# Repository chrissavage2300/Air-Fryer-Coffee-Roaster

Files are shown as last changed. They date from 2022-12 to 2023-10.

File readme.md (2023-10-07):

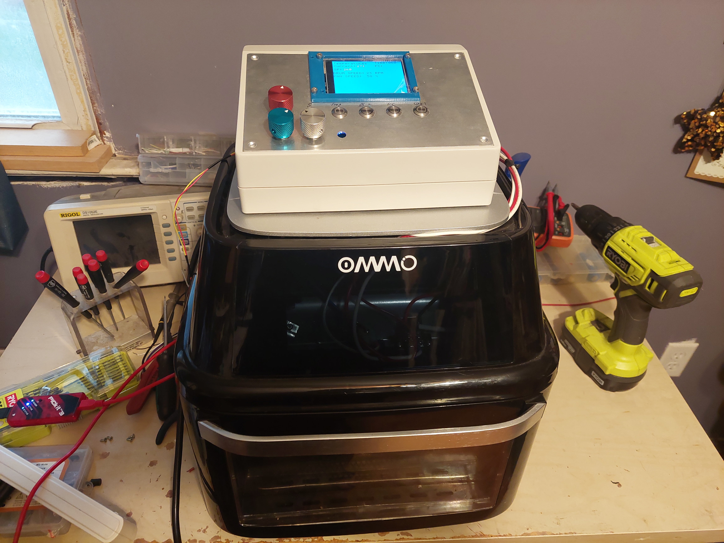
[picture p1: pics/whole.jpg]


A DIY Coffee roaster based on on air fryer. 

The idea is to have a rotating drum with a heater and fan inside. A nextion display will be used. 

Features:
Adjustable Temp
Adjustable Drum Speed
Adjustable Fan Speed
Cooling and heating modes

Change Log:

The roaster does work, but it has a slight issue when it gets hot where the rotation motor just doesnt turn. From what I can tell, its not a failure of the motor, but a fail in the comms. I have to look into why it does this, as i think its a buffer situation. Everything else works though, so Im not sure why just that gives out. 

10/7/2023- Uploaded Main Code

12/3/2022- Start of this github. But the project dates back a few months atleast

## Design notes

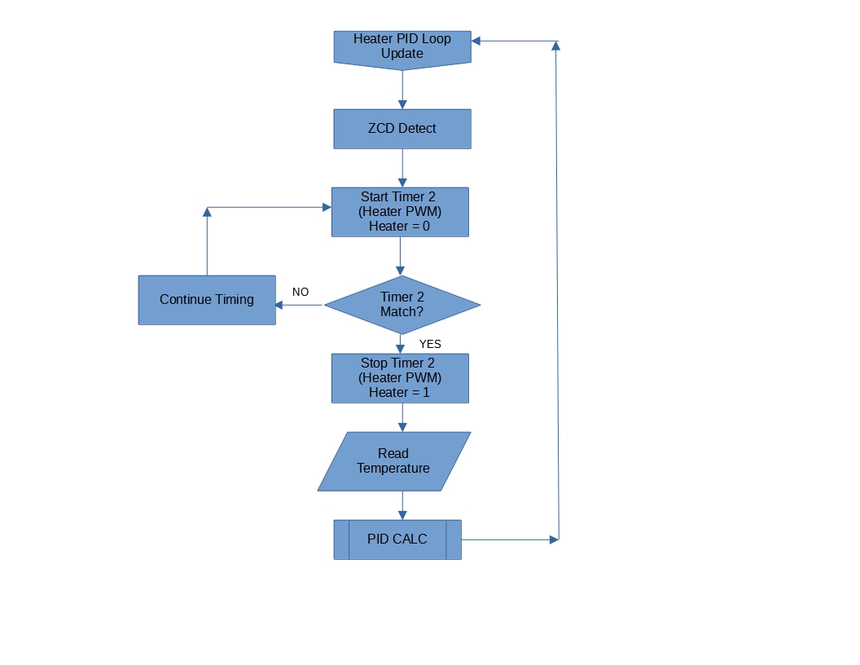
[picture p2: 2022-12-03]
code/ProgramFlowChart_2022_12_03_A_pg3.jpg

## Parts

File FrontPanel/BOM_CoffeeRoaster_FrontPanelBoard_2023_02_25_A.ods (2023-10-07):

Part | Value | Device | Package | Description
C1 | 22uF | CAP1206 | 1206 | Capacitor | CL31A226KPHNNNE/stock
C2 | 10uf | CAP1206 | 1206 | Capacitor | CL31A106KPHNNNE /stock
IC1 | AZ1117CR-3.3TRG1SOT89_AZ1117_DIO-M | AZ1117CR-3.3TRG1SOT89_AZ1117_DIO-M | SOT89_AZ1117_DIO-M |  | AZ1117CR-3.3TRG1/STOCK
IC2 | PIC16F18056-I/SO | PIC16F18056-I/SO | SOIC28-W_MC |  | STOCK
JP1 | DI | M08LOCK_LONGPADS | 1X08_LOCK_LONGPADS | Header 8 | ED10566-ND (https://www.digikey.com/en/products/detail/on-shore-technology-inc/OSTVN08A150/1588868)
JP2 | GLCD | M09LOCK-LONGPADS | 1X09_LOCK_LONGPADS | Header 9 | 2057-RS1-09-G-ND (https://www.digikey.com/en/products/detail/adam-tech/RS1-09-G/9832052)
JP4 | DO | M05LOCK_LONGPADS | 1X05_LOCK_LONGPADS | Header 5 | ED10564-ND (https://www.digikey.com/en/products/detail/on-shore-technology-inc/OSTVN05A150/1588865)
JP5 | ICSP | M05PTH | 1X05 | Header 5 | stock
JP6 | AI | M06LOCK_LONGPADS | 1X06_LOCK_LONGPADS | Header 6 | ED10565-ND (https://www.digikey.com/en/products/detail/on-shore-technology-inc/OSTVN06A150/1588866)
Q1 | MOSFET-NCHANNELBSS138 | MOSFET-NCHANNELBSS138 | SOT23-3 | Common NMOSFET Parts | IRLML6344TRPBF/STOCK
Q2 | MOSFET-NCHANNELBSS138 | MOSFET-NCHANNELBSS138 | SOT23-3 | Common NMOSFET Parts | IRLML6344TRPBF/STOCK
Q3 | MOSFET-NCHANNELBSS138 | MOSFET-NCHANNELBSS138 | SOT23-3 | Common NMOSFET Parts | IRLML6344TRPBF/STOCK
Q4 | MOSFET-NCHANNELBSS138 | MOSFET-NCHANNELBSS138 | SOT23-3 | Common NMOSFET Parts | IRLML6344TRPBF/STOCK
R1 | 10k | RESISTOR1206 | 1206 | Resistor | stock
R2 | 10k | RESISTOR1206 | 1206 | Resistor | stock
R3 | 10k | RESISTOR1206 | 1206 | Resistor | stock
R4 | 10k | RESISTOR1206 | 1206 | Resistor | stock
R5 | 10k | RESISTOR1206 | 1206 | Resistor | stock
R6 | 10k | RESISTOR1206 | 1206 | Resistor | stock
R7 | 10k | RESISTOR1206 | 1206 | Resistor | stock
R8 | 10k | RESISTOR1206 | 1206 | Resistor | stock
R9 | 10k | RESISTOR1206 | 1206 | Resistor | stock
R10 | 10k | RESISTOR1206 | 1206 | Resistor | stock
R11 | 50 | RESISTOR1206 | 1206 | Resistor | 47/STOCK
R12 | 50 | RESISTOR1206 | 1206 | Resistor | 47/STOCK
USARTIN |  | M04LONGPADS | 1X04_LONGPADS | Header 4 | ED10563-ND (https://www.digikey.com/en/products/detail/on-shore-technology-inc/OSTVN04A150/1588864)

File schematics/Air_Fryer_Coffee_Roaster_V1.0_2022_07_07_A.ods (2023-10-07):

 | Value | Device | Package | Description
BZ1 | CMI-1295-1285T | CMI-1295-1285T | CUI_CMI-1295-1285T | CUI Inc Buzzer Check availability | 102-CMI-1295-1285T-ND
C3 | 0.1uF | CAP0805 | 805 | Capacitor | 08055C104KAT4A/STOCK
C4 | 0.1uF | CAP0805 | 805 | Capacitor | 08055C104KAT4A/STOCK
C5 | 0.1u | CAP1206 | 1206 | Capacitor | CL31B104KBCNNNC/STOCK
C6 | 0.1u | CAP1206 | 1206 | Capacitor | CL31B104KBCNNNC/STOCK
C7 | 0.1u | CAP1206 | 1206 | Capacitor | CL31B104KBCNNNC/STOCK
C8 | 20uF,450V | CPOL-USE5-13 | E5-13 | POLARIZED CAPACITOR, American symbol | 450BXC22MEFC12.5X25
C9 | 270uF,16VDC | CAP_POLE | PANASONIC_E | Capacitor Polarized | EEE-HAE331UAP
C10 | 47uf | CAP_POLE | PANASONIC_E | Capacitor Polarized | EEE-1VA470P
C11 | 1nF,400VAC | C-US050-075X075 | C050-075X075 | CAPACITOR, American symbol | C907U102MYVDBA7317
D1 |  | DIODESOD-323F | SOD-323F | Diode | 1N4148WX-TP
D2 |  | DIODESOD-323F | SOD-323F | Diode | 1N4148WX-TP
F1 | 16A | FUSE | FUSE | FUSE | 696108003002 696122003001
HEATER_FAN | M025MM | M025MM | SCREWTERMINAL-5MM-2 | Standard 2-pin 0.1 | 1935161
IC1 | AZ1117C | ADP3338AKCZ-5-R7 | SOT230P700X180-4N | Low Dropout Regulator | AZ1117CH-5.0TRG1DICT-ND
IC2 | AZ1117CR-3.3TRG1 | AZ1117CR-3.3TRG1 | SOT89_AZ1117_DIO |  | AZ1117CR-3.3TRG1DICT-ND
IC3 | PIC16F18446-I/SOSOIC20_SO_MCH-M | PIC16F18446-I/SOSOIC20_SO_MCH-M | SOIC20_SO_MCH-M |  | stock
ISO1 | MOC3021SMOC3021S_LTO-M | MOC3021SMOC3021S_LTO-M | MOC3021S_LTO-M |  | MOC3021S
ISO2 | LTV-814S-TA1 | SFH6206 | DIL4-SMD | Optocoupler, Phototransistor Output, AC Input | LTV-814S-TA1
ISO4 | MOC3021SMOC3021S_LTO-M | MOC3021SMOC3021S_LTO-M | MOC3021S_LTO-M |  | MOC3021S
JP1 | ICSP | M05PTH | 1X05 | Header 5
JP2 |  | M02POLAR_LOCK | MOLEX-1X2_LOCK | Header 2
JP3 |  | M02POLAR_LOCK | MOLEX-1X2_LOCK | Header 2
JP5 | UART | M04LOCK | 1X04_LOCK | Header 4
L1 | 4.7uH, 2.2A | SRR1260-100M | IND_BOURNS_SRR1260 |  | NRS5040T4R7NMGK
LED1 | GRN | LED1206 | LED-1206 | LEDs | 732-4993-1-ND/ STOCK
LED2 | YELLOW | LED1206 | LED-1206 | LEDs | 732-4994-1-ND/STOCK
LED3 | GRN | LED1206 | LED-1206 | LEDs | 732-4993-1-ND/ STOCK
LED5 | BLUE | LED1206 | LED-1206 | LEDs | 732-4989-1-ND/STOCK
PIN | M025MM | M025MM | SCREWTERMINAL-5MM-2 | Standard 2-pin 0.1 | 1935161
POUT | M025MM | M025MM | SCREWTERMINAL-5MM-2 | Standard 2-pin 0.1 | 1935161
PS1 | LS05-13B12R3 | LS05-13B12R3 | CONV_LS05-13B12R3 |  | 2725-LS05-13B12R3-ND (https://www.digikey.com/en/products/detail/mornsun-america-llc/LS05-13B12R3/13531111)
Q1 | IRLML6344TRPBF | MOSFET-NCHANNEL2N7002PW | SOT323 | Common NMOSFET Parts | IRLML6344TRPBFCT-ND/ STOCK
Q2 | IRLML6344TRPBF | MOSFET-NCHANNEL2N7002PW | SOT323 | Common NMOSFET Parts | IRLML6344TRPBFCT-ND/ STOCK
Q3 | IRLML6344TRPBF | MOSFET-NCHANNEL2N7002PW | SOT323 | Common NMOSFET Parts | IRLML6344TRPBFCT-ND/ STOCK
R1 | 200 | R-US_R2512 | R2512 | RESISTOR, American symbol | CRM2512AJW-201ELFCT-ND
R2 | 6.19k | R-US_R2512 | R2512 | RESISTOR, American symbol | ERJ-1TNF6191U
R3 | 6.19k | R-US_R2512 | R2512 | RESISTOR, American symbol | ERJ-1TNF6191U
R4 | 220 | RESISTOR1206 | 1206 | Resistor | stock
R5 | 200 | R-US_R2512 | R2512 | RESISTOR, American symbol | CRM2512AJW-201ELFCT-ND
R6 | 220 | RESISTOR1206 | 1206 | Resistor | stock
R7 | 6.19k | R-US_R2512 | R2512 | RESISTOR, American symbol | ERJ-1TNF6191U
R8 | 10k | R-US_M0805 | M0805 | RESISTOR, American symbol | RNCP0805FTD10K0
R9 | 10k | R-US_M0805 | M0805 | RESISTOR, American symbol | RNCP0805FTD10K0
R10 | 340 | RESISTOR1206 | 1206 | Resistor
R15 | 2k | RESISTOR1206 | 1206 | Resistor | stock
R16 | 2k | RESISTOR1206 | 1206 | Resistor | stock
R19 | 340 | RESISTOR1206 | 1206 | Resistor
R20 | 10k | RESISTOR1206 | 1206 | Resistor | stock
T1 | BT138-600,127 | BT138-V | TO220BV | TRIAC | BT139-600E/DG,127
T2 | TRIACSMD | TRIACSMD | SOT223 |  | Z0107MN,135
TS1 | YK3210203000G | 282845-2 | CONN2_282845-2_TEC |  | YK3210203000G
U1 | MAX31855JASA | MAX31855JASA+21-0041B_8_MXM-M | 21-0041B_8_MXM-M

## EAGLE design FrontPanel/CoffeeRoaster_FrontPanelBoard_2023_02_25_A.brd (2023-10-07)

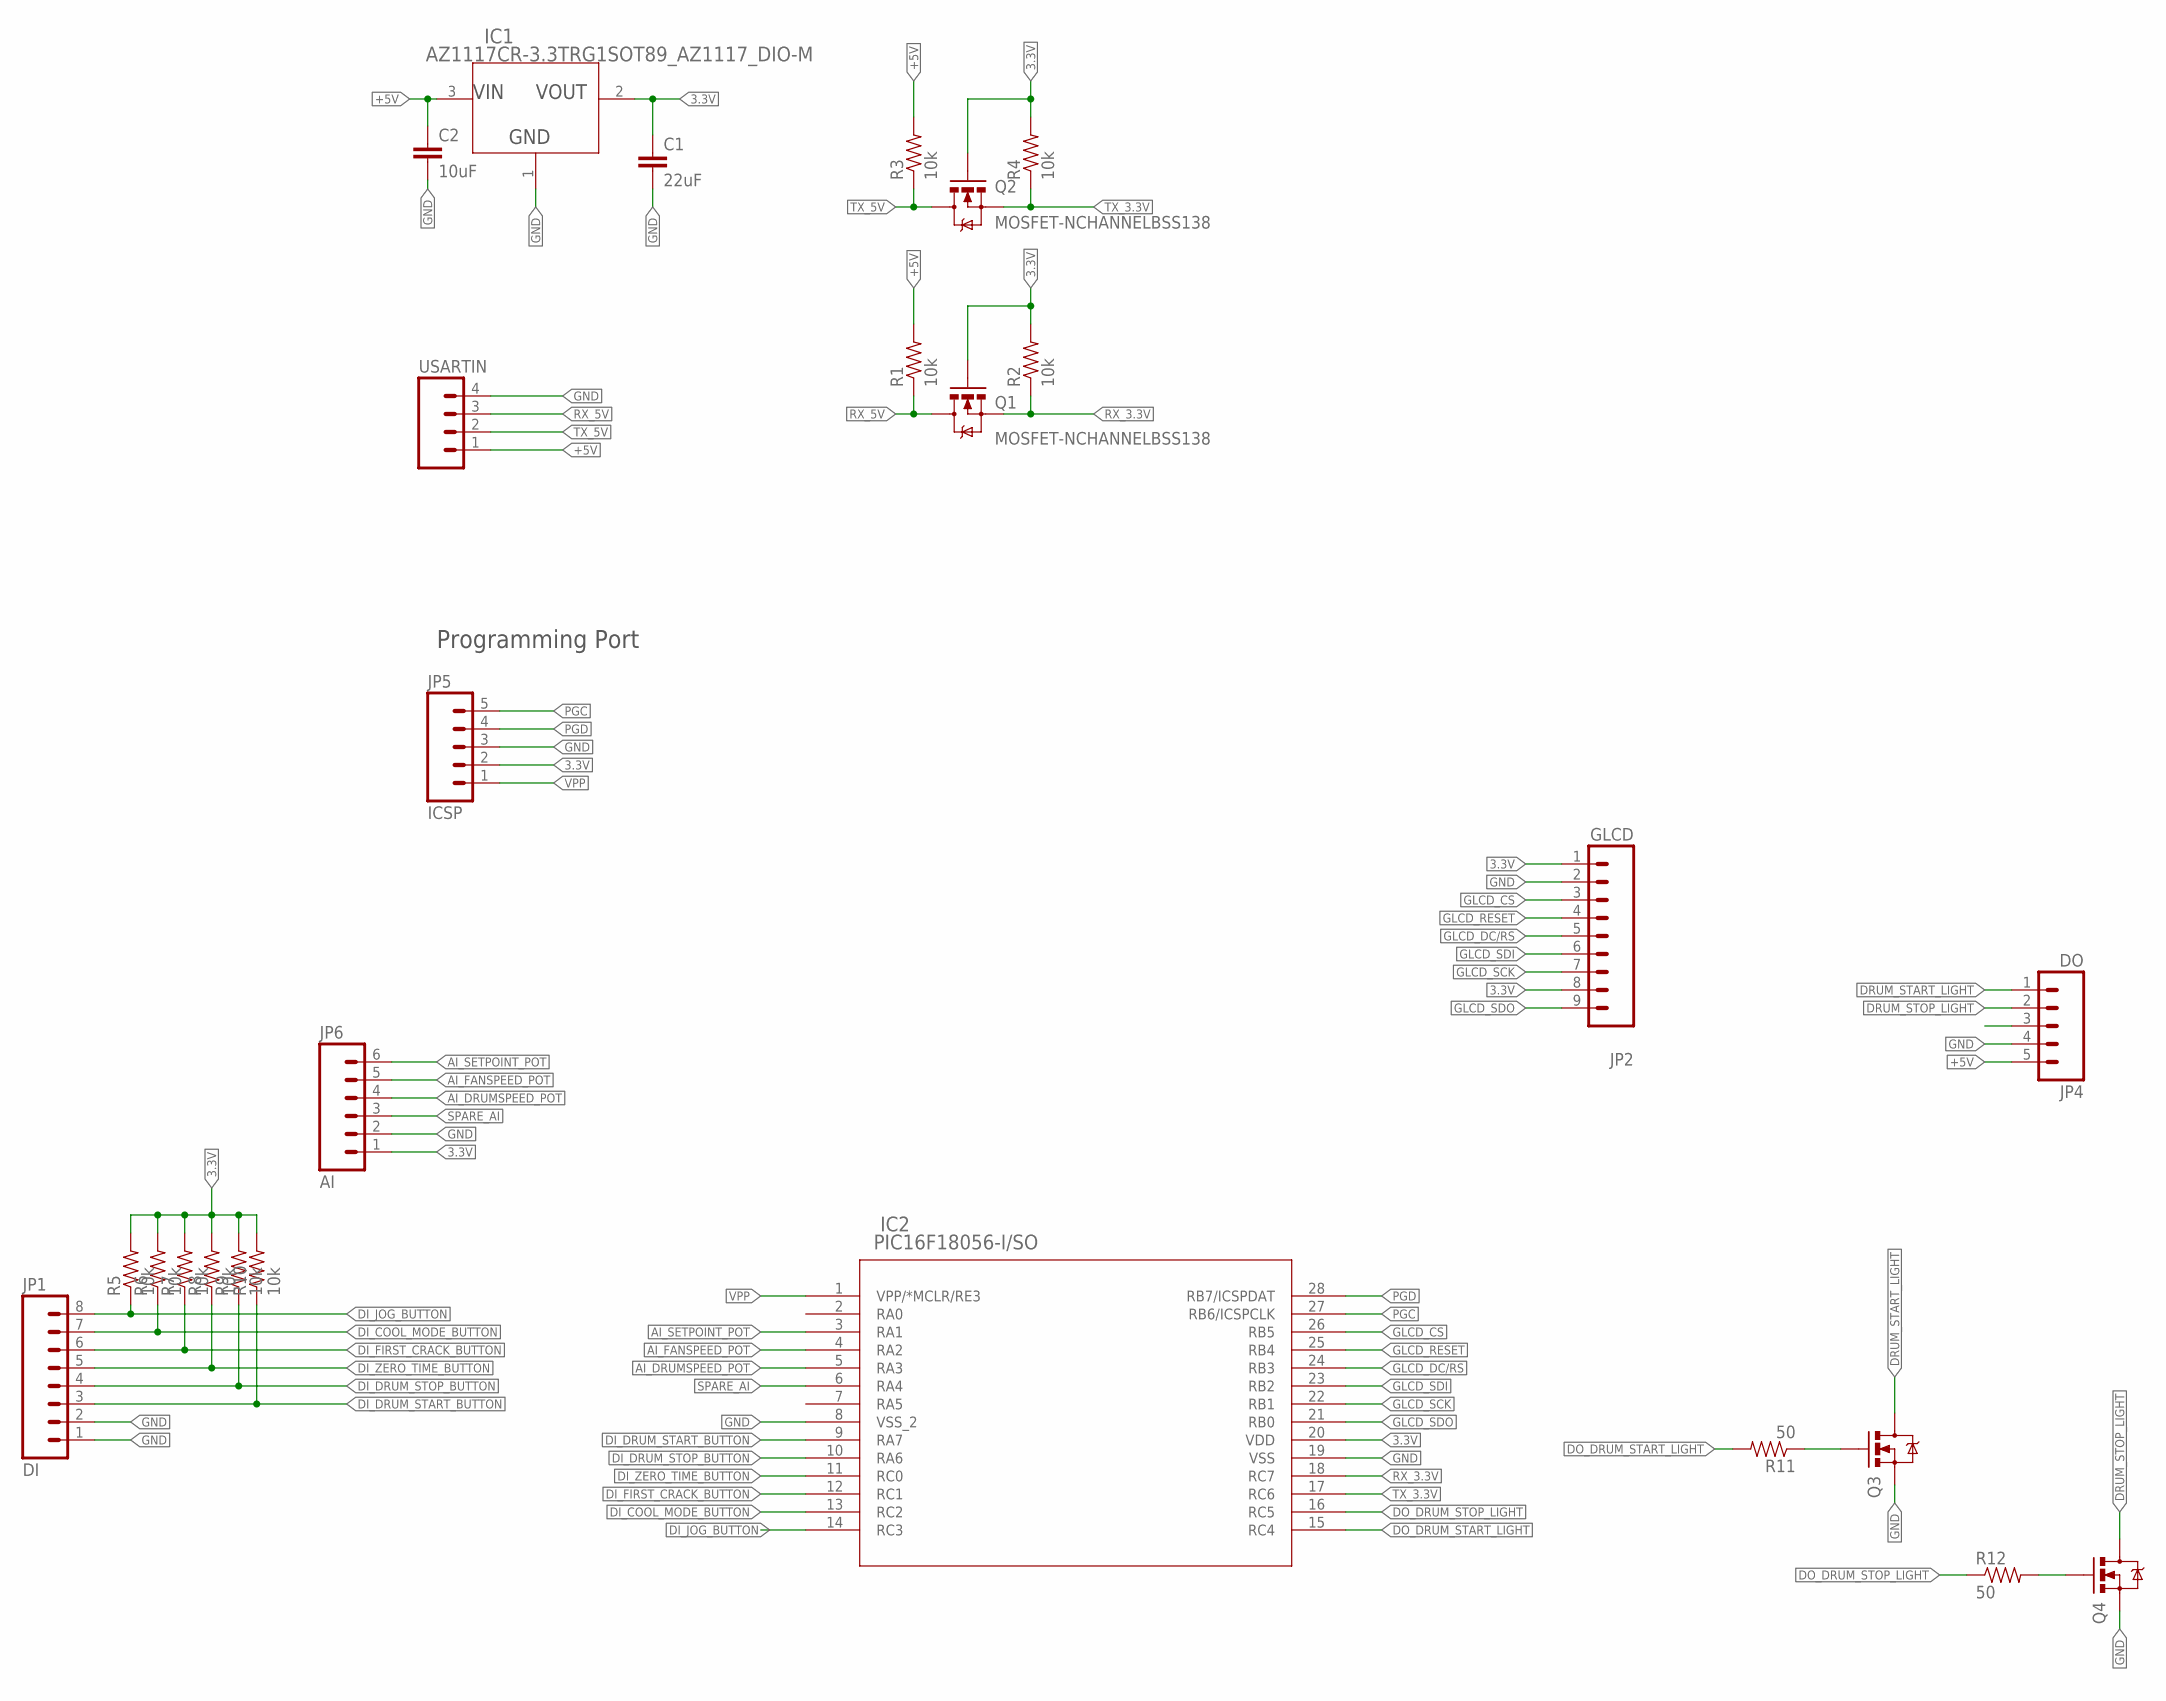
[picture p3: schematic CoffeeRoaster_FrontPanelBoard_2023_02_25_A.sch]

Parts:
C1: 22uF; 1206
C2: 10uF; 1206
IC1: AZ1117CR-3.3TRG1SOT89_AZ1117_DIO-M; SOT89_AZ1117_DIO-M
IC2: PIC16F18056-I/SO; SOIC28-W_MC
JP1: DI; 1X08_LOCK_LONGPADS
JP2: GLCD; 1X09_LOCK_LONGPADS
JP4: DO; 1X05_LOCK_LONGPADS
JP5: ICSP; 1X05
JP6: AI; 1X06_LOCK_LONGPADS
Q1, Q2, Q3, Q4: MOSFET-NCHANNELBSS138; SOT23-3
R1, R2, R3, R4, R5, R6, R7, R8, R9, R10: 10k; 1206
R11, R12: 50; 1206
USARTIN: M04LONGPADS; 1X04_LONGPADS

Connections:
3.3V: C1.1, IC1.2 (OUTPUT), IC2.20 (VDD), JP2.1, JP2.8, JP5.2, JP6.1, Q1.1 (G), Q2.1 (G), R2.2, R4.2, R5.2, R6.2, R7.2, R8.2, R9.2, R10.2
+5V: C2.1, IC1.3 (INPUT), JP4.5, R1.2, R3.2, USARTIN.1
AI_DRUMSPEED_POT: IC2.5 (RA3), JP6.4
AI_FANSPEED_POT: IC2.4 (RA2), JP6.5
AI_SETPOINT_POT: IC2.3 (RA1), JP6.6
DI_COOL_MODE_BUTTON: IC2.13 (RC2), JP1.7, R6.1
DI_DRUM_START_BUTTON: IC2.9 (RA7), JP1.3, R10.1
DI_DRUM_STOP_BUTTON: IC2.10 (RA6), JP1.4, R9.1
DI_FIRST_CRACK_BUTTON: IC2.12 (RC1), JP1.6, R7.1
DI_JOG_BUTTON: IC2.14 (RC3), JP1.8, R5.1
DI_ZERO_TIME_BUTTON: IC2.11 (RC0), JP1.5, R8.1
DO_DRUM_START_LIGHT: IC2.15 (RC4), R11.2
DO_DRUM_STOP_LIGHT: IC2.16 (RC5), R12.1
DRUM_START_LIGHT: JP4.1, Q3.3 (D)
DRUM_STOP_LIGHT: JP4.2, Q4.3 (D)
GLCD_CS: IC2.26 (RB5), JP2.3
GLCD_DC/RS: IC2.24 (RB3), JP2.5
GLCD_RESET: IC2.25 (RB4), JP2.4
GLCD_SCK: IC2.22 (RB1), JP2.7
GLCD_SDI: IC2.23 (RB2), JP2.6
GLCD_SDO: IC2.21 (RB0), JP2.9
GND: C1.2, C2.2, IC1.1 (ADJ/GND), IC2.8 (VSS_2), IC2.19 (VSS), JP1.1, JP1.2, JP2.2, JP4.4, JP5.3, JP6.2, Q3.2 (S), Q4.2 (S), USARTIN.4
unnamed: Q3.1 (G), R11.1
unnamed: Q4.1 (G), R12.2
PGC: IC2.27 (RB6/ICSPCLK), JP5.5
PGD: IC2.28 (RB7/ICSPDAT), JP5.4
RX_3.3V: IC2.18 (RC7), Q1.2 (S), R2.1
RX_5V: Q1.3 (D), R1.1, USARTIN.3
SPARE_AI: IC2.6 (RA4), JP6.3
TX_3.3V: IC2.17 (RC6), Q2.2 (S), R4.1
TX_5V: Q2.3 (D), R3.1, USARTIN.2
VPP: IC2.1 (VPP/*MCLR/RE3), JP5.1

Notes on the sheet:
Programming Port

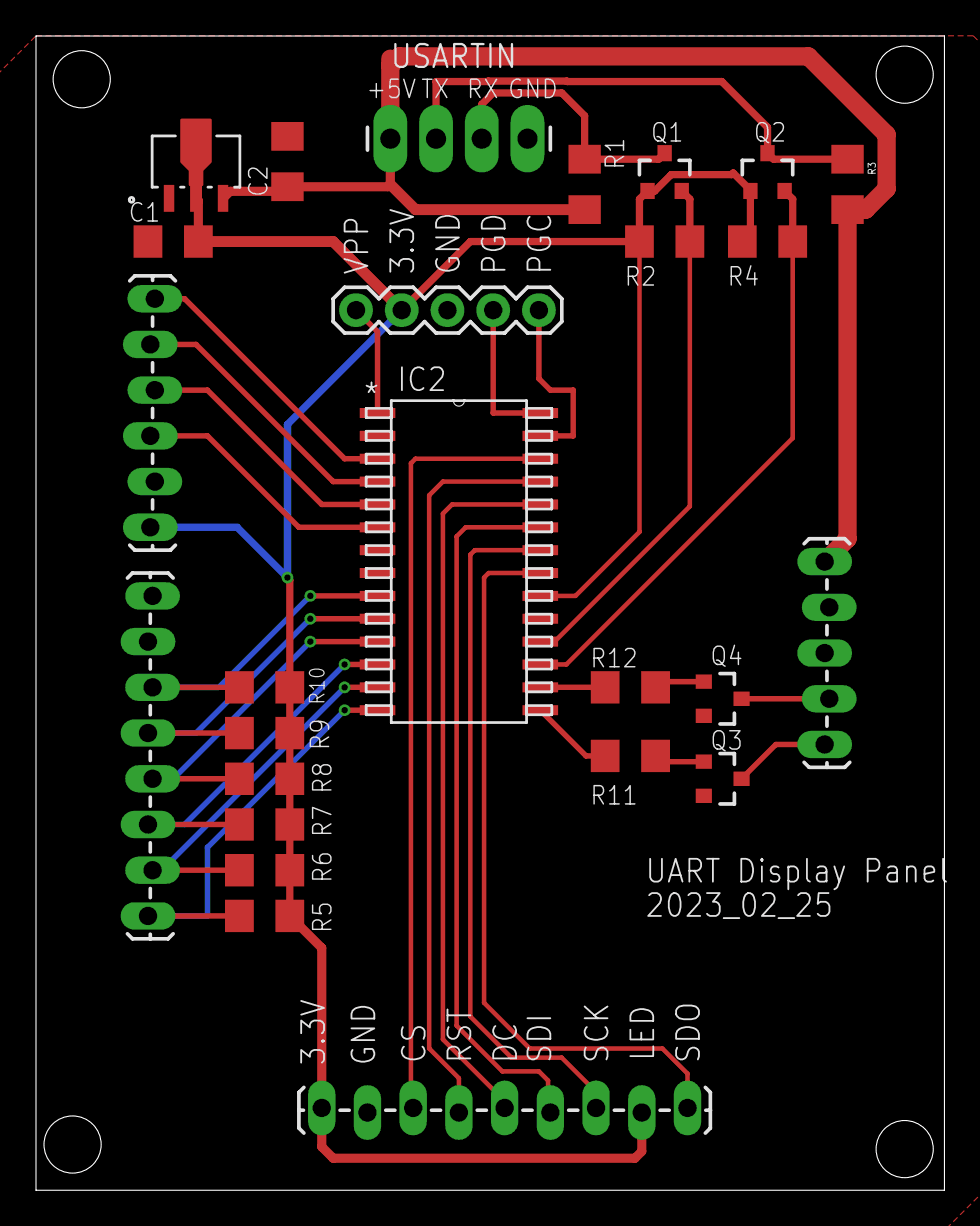
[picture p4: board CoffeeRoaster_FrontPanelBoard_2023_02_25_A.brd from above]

Board: 2 copper layers, 50.5 x 64.1 mm, 26 parts (0 on the bottom side), 32 nets.

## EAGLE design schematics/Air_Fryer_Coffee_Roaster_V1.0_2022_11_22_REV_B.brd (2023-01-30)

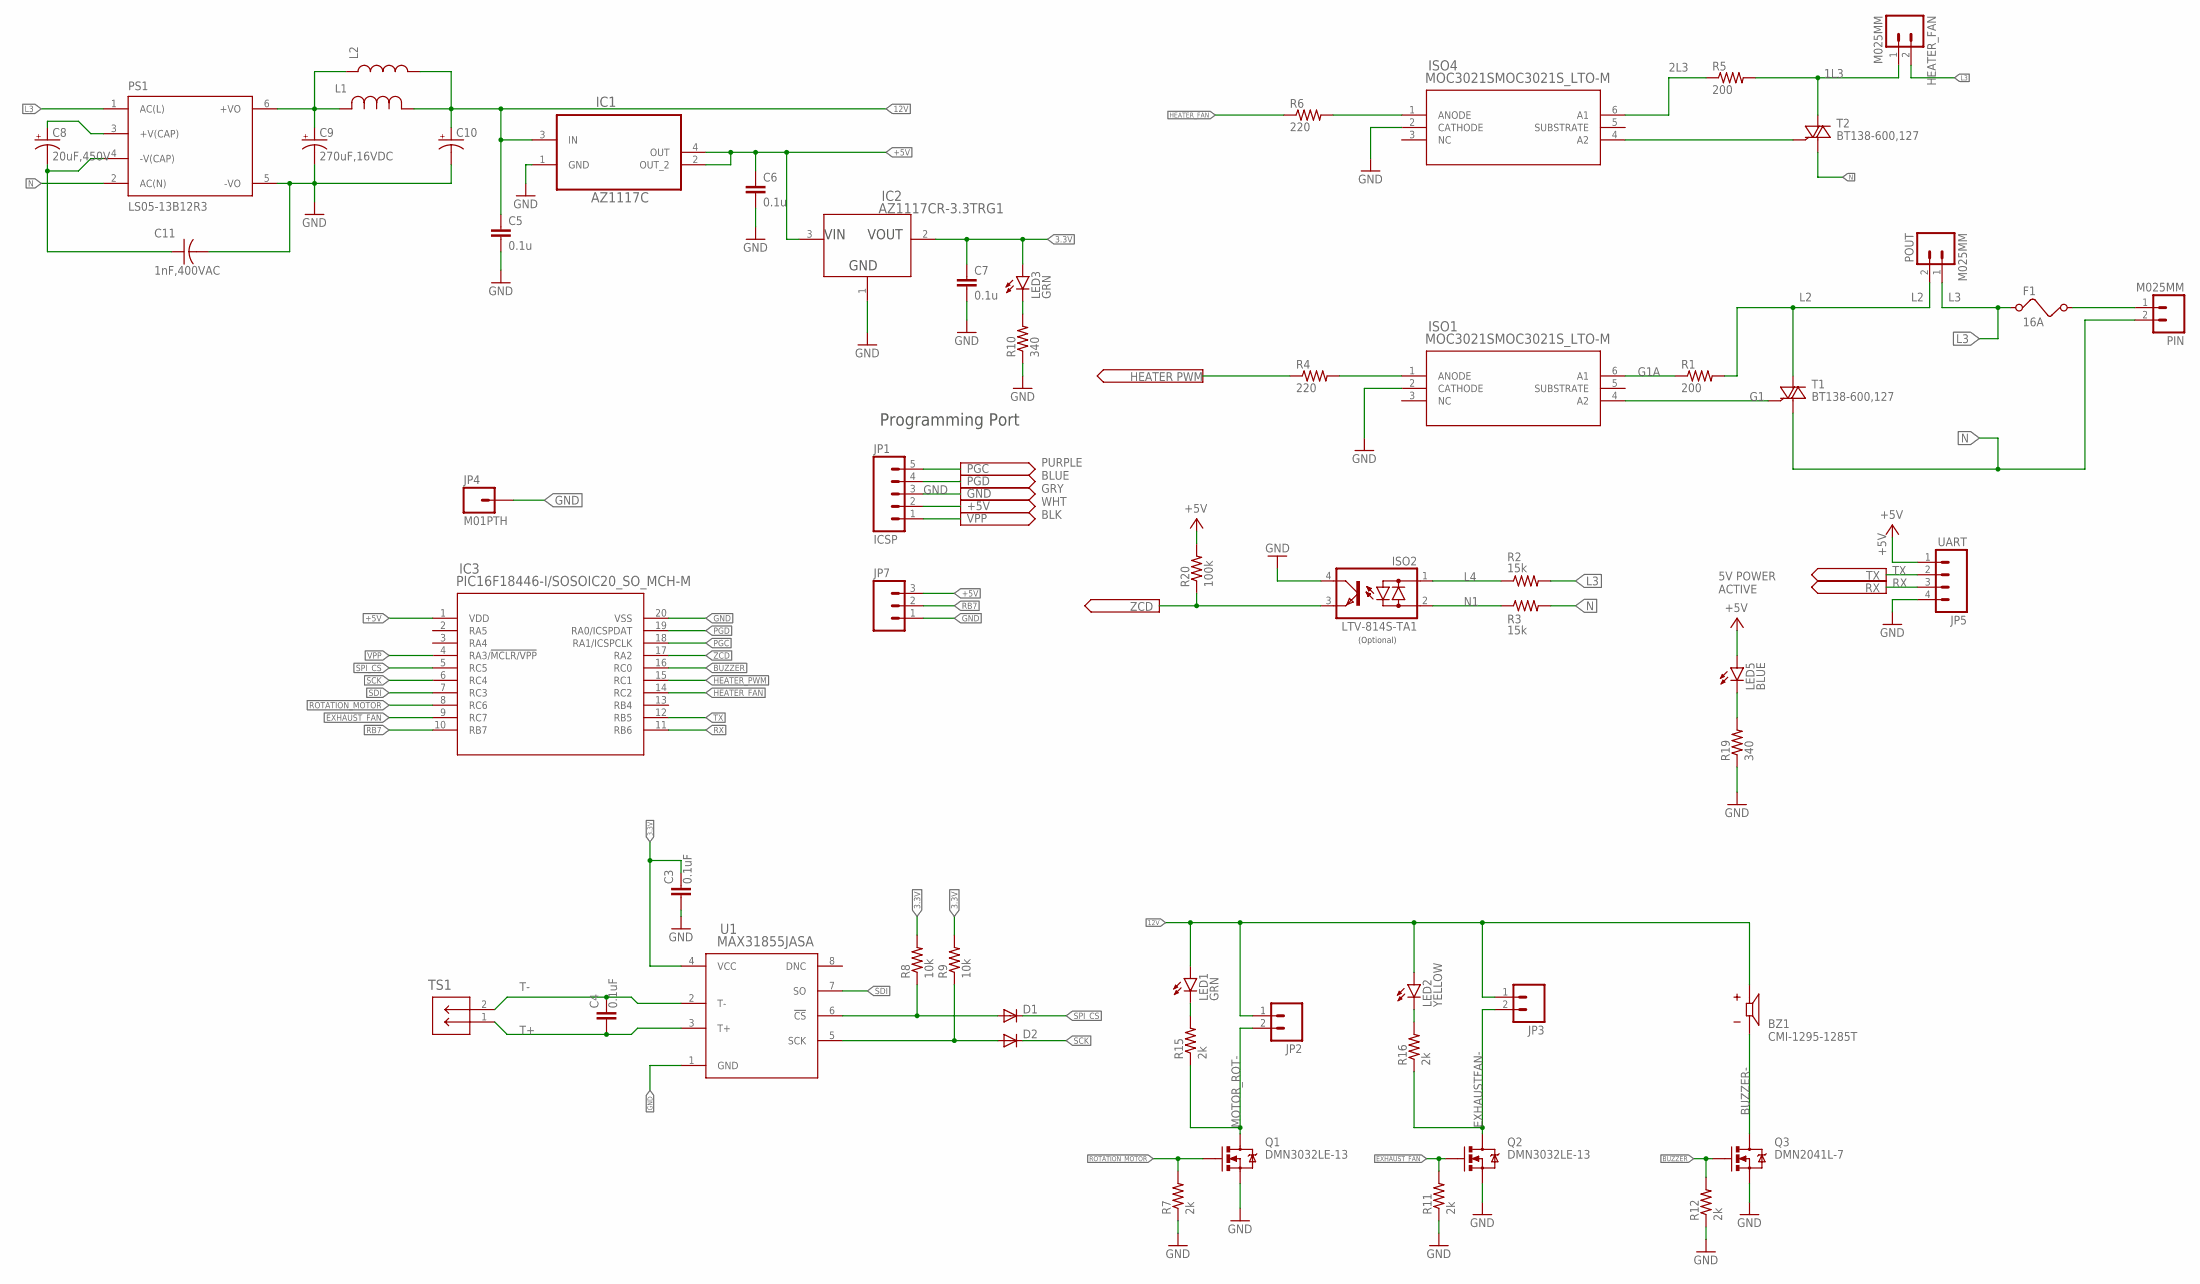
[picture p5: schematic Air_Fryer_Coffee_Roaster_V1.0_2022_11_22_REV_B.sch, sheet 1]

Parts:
BZ1: CMI-1295-1285T; CUI_CMI-1295-1285T
C3, C4: 0.1uF; 0805
C5, C6, C7: 0.1u; 1206
C8: 20uF,450V; E5-13
C9: 270uF,16VDC; PANASONIC_E
C10: CAP_POLE; PANASONIC_E
C11: 1nF,400VAC; C050-075X075
D1, D2: DIODESOD-323F; SOD-323F
F1: 16A; FUSE
HEATER_FAN: M025MM; SCREWTERMINAL-5MM-2
IC1: AZ1117C; SOT230P700X180-4N
IC2: AZ1117CR-3.3TRG1; SOT89_AZ1117_DIO
IC3: PIC16F18446-I/SOSOIC20_SO_MCH-M; SOIC20_SO_MCH-M
ISO1, ISO4: MOC3021SMOC3021S_LTO-M; MOC3021S_LTO-M
ISO2: LTV-814S-TA1; DIL4-SMD
JP1: ICSP; 1X05
JP2, JP3: M02POLAR_LOCK; MOLEX-1X2_LOCK
JP4: M01PTH; 1X01
JP5: UART; 1X04_LOCK
JP7: M03LOCK; 1X03_LOCK
L1: 4.7uH, 2.2A; IND_BOURNS_SRR1260
L2: INDUCTORCR54; CR54
LED1, LED3: GRN; LED-1206
LED2: YELLOW; LED-1206
LED5: BLUE; LED-1206
PIN: M025MM; SCREWTERMINAL-5MM-2
POUT: M025MM; SCREWTERMINAL-5MM-2
PS1: LS05-13B12R3; CONV_LS05-13B12R3
Q1, Q2: DMN3032LE-13; SOT223
Q3: DMN2041L-7; SOT23-3
R1, R5: 200; R2512
R2, R3: 15k; R2512
R4, R6: 220; 1206
R7, R11, R12, R15, R16: 2k; 1206
R8, R9: 10k; M0805
R10, R19: 340; 1206
R20: 100k; 1206
T1, T2: BT138-600,127; TO220BV
TS1: YK3210203000G; CONN2_282845-2_TEC
U1: MAX31855JASA; 21-0041B_8_MXM-M

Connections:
1L3: HEATER_FAN.1, R5.2, T2.T2 (A2)
2L3: ISO4.6 (A1), R5.1
3.3V: C3.2, C7.1, IC2.2 (OUTPUT), LED3.A, R8.2, R9.2, U1.4 (VCC)
12V: BZ1.P, C5.1, C10.+, IC1.3 (IN), JP2.1, JP3.1, L1.1, L2.P$2 (2), LED1.A, LED2.A
+5V: C6.1, IC1.2 (OUT_2), IC1.4 (OUT), IC2.3 (INPUT), IC3.1 (VDD), JP1.2, JP5.1, JP7.3, LED5.A, R20.2
BUZZER: IC3.16 (RC0), Q3.1 (G), R12.2
BUZZER-: BZ1.N, Q3.3 (D)
EXHAUSTFAN-: JP3.2, Q2.2 (D), Q2.4 (D), R16.1
EXHAUST_FAN: IC3.9 (RC7), Q2.1 (G), R11.2
G1: ISO1.4 (A2), T1.G
G1A: ISO1.6 (A1), R1.1
GATE_2: ISO4.4 (A2), T2.G
GND: C3.1, C5.2, C6.2, C7.2, C9.-, C10.-, C11.2, IC1.1 (GND), IC2.1 (ADJ/GND), IC3.20 (VSS), ISO1.2 (CATHODE), ISO2.4 (C), ISO4.2 (CATHODE), JP1.3, JP4.1, JP5.4, JP7.1, PS1.5 (-VO), Q1.3 (S), Q2.3 (S), Q3.2 (S), R7.1, R10.1, R11.1, R12.1, R19.1, U1.1 (GND)
HEATER_FAN: IC3.14 (RC2), R6.1
HEATER_PWM: IC3.15 (RC1), R4.1
L1: F1.2, PIN.1
L2: POUT.2, R1.2, T1.T2 (A2)
L3: F1.1, HEATER_FAN.2, POUT.1, PS1.1 (AC(L)), R2.2
L4: ISO2.1 (AC1), R2.1
MOTOR_ROT-: JP2.2, Q1.2 (D), Q1.4 (D), R15.1
N: PIN.2, PS1.2 (AC(N)), R3.2, T1.T1 (A1), T2.T1 (A1)
N1: ISO2.2 (AC2), R3.1
unnamed: ISO1.1 (ANODE), R4.2
unnamed: LED3.C, R10.2
unnamed: LED1.C, R15.2
unnamed: LED2.C, R16.2
unnamed: C8.+, PS1.3 (+V(CAP))
unnamed: C8.-, C11.1, PS1.4 (-V(CAP))
unnamed: ISO4.1 (ANODE), R6.2
unnamed: D1.A, R8.1, U1.6 (!CS)
unnamed: LED5.C, R19.2
unnamed: D2.A, R9.1, U1.5 (SCK)
unnamed: C9.+, L1.2, L2.P$1 (1), PS1.6 (+VO)
PGC: IC3.18 (RA1/ICSPCLK), JP1.5
PGD: IC3.19 (RA0/ICSPDAT), JP1.4
RB7: IC3.10 (RB7), JP7.2
ROTATION_MOTOR: IC3.8 (RC6), Q1.1 (G), R7.2
RX: IC3.11 (RB6), JP5.3
SCK: D2.C, IC3.6 (RC4)
SDI: IC3.7 (RC3), U1.7 (SO)
SPI_CS: D1.C, IC3.5 (RC5)
T+: C4.1, TS1.1, U1.3 (T+)
T-: C4.2, TS1.2, U1.2 (T-)
TX: IC3.12 (RB5), JP5.2
VPP: IC3.4 (RA3/!MCLR/VPP), JP1.1
ZCD: IC3.17 (RA2), ISO2.3 (E), R20.1

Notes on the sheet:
Programming Port
5V POWER ACTIVE
PURPLE BLUE GRY WHT BLK
(Optional)

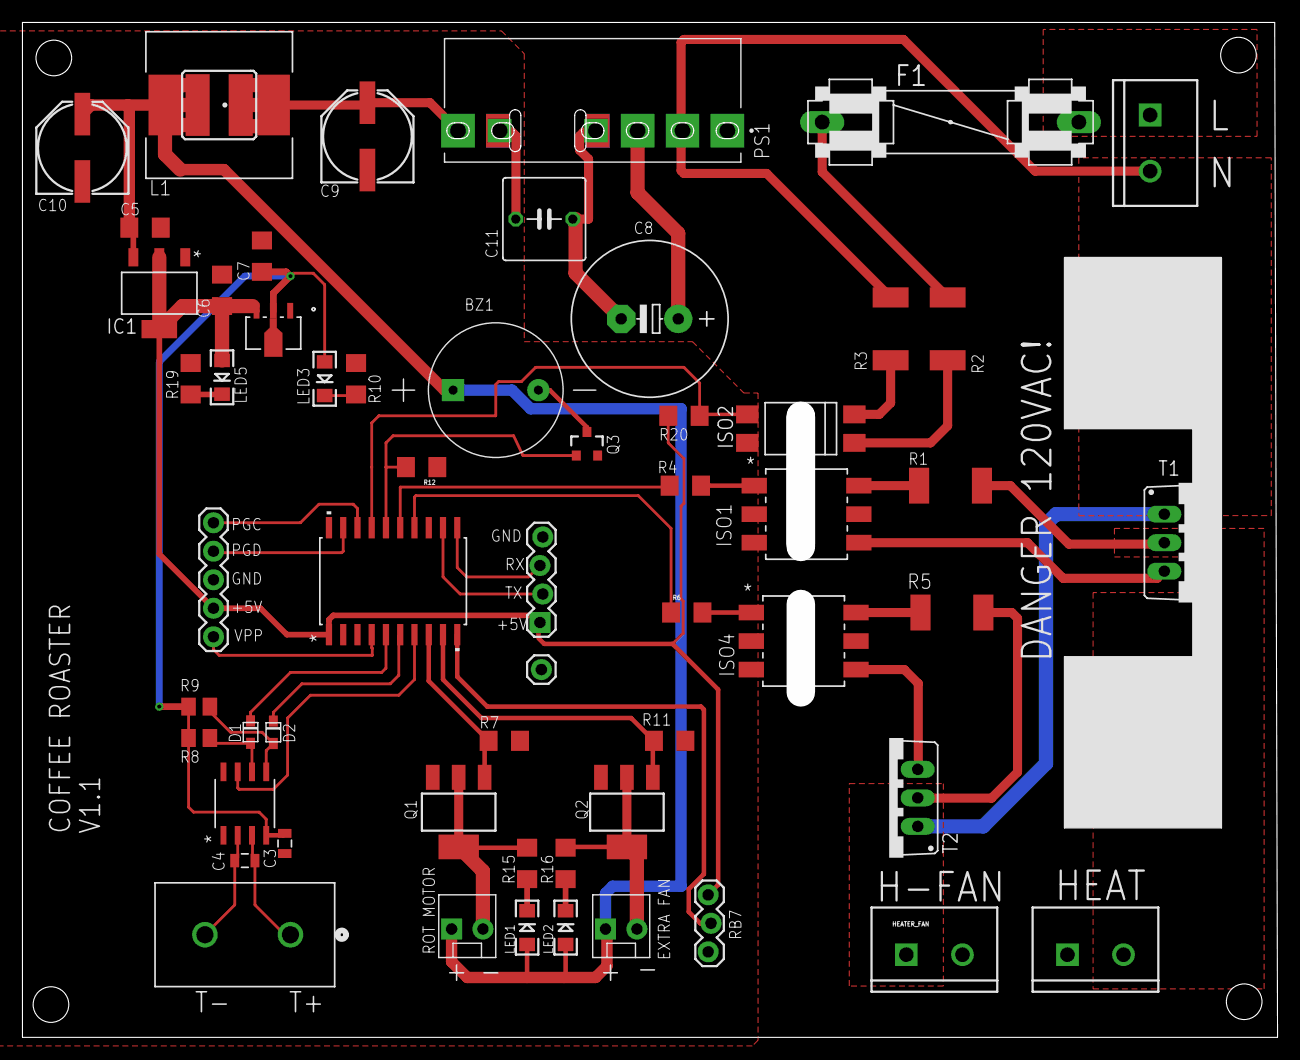
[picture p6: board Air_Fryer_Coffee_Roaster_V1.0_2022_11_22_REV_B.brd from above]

Board: 2 copper layers, 111.8 x 90.4 mm, 59 parts (0 on the bottom side), 46 nets.

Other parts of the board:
HEATSINK: 7-345-2PP-BA

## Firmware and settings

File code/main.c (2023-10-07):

/**
 * Coffee Roasting Control Board Software
 * 
 * 2023/02/10 
 * 
 * Heater Fan in Rev 1 is relay controlled
 * 
*/

#include "mcc_generated_files/mcc.h"
#include <stdio.h>
#include <string.h>


//SPI Vars
uint8_t writeData = 1; /* Data that will be transmitted */
uint8_t SPI_receiveData; /* Data that will be received */
uint8_t SPI_receiveData2;
uint8_t SPI_receiveData3;
uint8_t SPI_receiveData4;
unsigned int CurrentTemperature;
unsigned int TempVariable;
unsigned int ScaledTempF;
unsigned int ScaledTempHMI;

//PID loop vars
extern unsigned int DerivativeTime;  //external variable used in tmr1.c
signed int Intergral;
signed int Error;
//signed int PreviousError;
//signed char Derivative;
unsigned int SetTemperature;//
unsigned int PIDoutput;
unsigned int PIDinterm;
_Bool IntakeFanBit;

//PID control
extern unsigned char PID;
signed int ki_term;
signed int kp_term;


//make constants negative to invert output
//PID Constants
const signed int Kp = 12;//
const signed int Ki = 0;//
//const signed int Kd = 1;


//USART Vars
char buf[8];
extern uint8_t eusart1RxBuffer[8];
unsigned char COOL;
unsigned char HEAT;
unsigned char CLEARTIME;
unsigned char TEMP_MINUS;
unsigned char TEMP_PLUS;
unsigned char Fan_MINUS;
unsigned char Fan_PLUS;
unsigned char Rot_MINUS;
unsigned char Rot_PLUS;
unsigned char Rot_ON;
unsigned char Rot_OFF;
unsigned char FIRSTCRACK;

unsigned char NUMBERINPUT;
char IntBuffer[3];
unsigned int val;

unsigned char USART_TemperatureSP_Compare;
unsigned char USART_FanSPSP_Compare;
unsigned char USART_DrumSP_Compare;

//scaling vars
//PWM Scale calc: ((X * 2) + 745)/10 scales RPM input to PWM output
//PWM min = 76 (80%)), ~7RPM
//PWM max = 99 (100%), ~120 RPM
unsigned int RPM;
unsigned int RPM_Scaled;

//Fan Speed scaling
//Fan uses Timer 6
//160 is heater fan min
//0 is fully on
// therefore: (-1.6*X) + 160
//fanspeed is the requested speed. (0 to 100%))
//Fanspeed_scaled is the output to the timer
extern signed int Fanspeed=50;
extern unsigned char Fanspeed_Scaled;
unsigned char Old_Fanspeed;


//misc
extern unsigned int Elapsed_Time=0;//seconds
extern unsigned int Cooling_Time=0;//seconds
unsigned int Set_Time=1200;//seconds
extern _Bool RoastFinished=0;
extern _Bool CoolingMode=0;
extern _Bool CoolingSecondsBit=0;
unsigned char GarbageByte;
unsigned int StartupFinished=0;
extern unsigned char DisplayDelaytime=0;
unsigned int FirstCrackTime;

extern _Bool Overtemp;
extern _Bool ROTARTY_ON;

/*
                         Main application
 */

unsigned char PIDLoop(){//NOT USED CURRENTLY
    
//        //NOTE Higher values mean less of the sine wave gets passed
//        //PID = 0 is a full sine wave, PID = 255 is fully OFF
//        //IF INVERETED THIS IS REVERSE
//        //PIE3bits.RC1IE = 0;
//        Error = SetTemperature - ScaledTempHMI;
//        Intergral = Intergral + Error;
////        if (Error <=1){IntakeFanBit=1;EXHAUST_FAN_SetHigh();}//turn on the fan and bring in some fresh air
////        if (Error > 1){IntakeFanBit=0; EXHAUST_FAN_SetLow();}
//         //check Intergral error to make sure it doesnt get too large
//        if (Intergral >= 255){Intergral=255;}
//        if (Intergral <= -255){Intergral=-255;}            
//        
//        //Derivative = (Error - PreviousError)/DerivativeTime;
//        Derivative = (Error - PreviousError);   
//
//        
//        PIDoutput = (Error/Kp) + (Intergral*Ki) + (Derivative*Kd);            
//        //PIDoutput=~PIDoutput;
//        if (PIDoutput <= 0){PIDoutput=0;}
//        PreviousError = Error; 
//        return PIDoutput;   
//}


//Functions not used:
//void NextionBasic_command(char *Text) //basic command to get started.
//{
//    printf(Text);
//    EUSART1_Write(0xFF);
//    EUSART1_Write(0xFF);
//    EUSART1_Write(0xFF);
//    
//}
////This command sends a string and a number to a number box in the Nextion HMI
////so if you have a number box called "n0", the commands will be used like this:
////NextionSendNumber_command("n0.val=",i2);
////assuming i2 is an unsigned int
//void NextionSendNumber_command(char *Text,unsigned int number) 
//{
//        // disable receive interrupt
//    //PIE3bits.RC1IE = 0;
//    printf(Text);
//    printf("%d",number);
//    EUSART1_Write(0xFF);
//    EUSART1_Write(0xFF);
//    EUSART1_Write(0xFF);    
//        // enable receive interrupt
//    //PIE3bits.RC1IE = 1;
} 

void EUSART_Read_Text(char *Output, unsigned int length)
{
	unsigned int j;
	for(j=0;j<length;j++)
	Output[j] = EUSART1_Read();
}

void main(void)
{
    // initialize the device
    SYSTEM_Initialize();

    // Enable the Global Interrupts
    INTERRUPT_GlobalInterruptEnable();

    // Enable the Peripheral Interrupts
    INTERRUPT_PeripheralInterruptEnable();
        SPI1_Initialize();
        PWM6_Initialize();
                TMR2_Initialize();
        TMR2_Stop();

     
    PWM6EN=0;
    memset(buf,0,8);//clear buffer after
    SetTemperature = 450;
    //PIDoutput = 128;//set initial
    
    while (1)
    {
        



        //scale the RPM for the rotary drum.        
        RPM_Scaled = (((RPM*2)+746)/10);
        //This turns on and off the rotary drum
        //PWM6EN=1;//PWM6EN=0;
        PWM6_LoadDutyValue(RPM_Scaled);        
        Fanspeed_Scaled=(((Fanspeed*-10)+1600)/10);
       
        
        //MAX31885 notes: Last TWO bits of receiveData2 have to be dropped
        // in order to convert things. Then the number has to be multiplied by 0.25
        //OR shift to the right two times. 
        SPI1_Open(SPI1_DEFAULT);
        CS_SetLow();

        SPI_receiveData = SPI1_ExchangeByte(writeData);
        SPI_receiveData2 = SPI1_ExchangeByte(writeData);
        SPI_receiveData3 = SPI1_ExchangeByte(writeData);
        SPI_receiveData4 = SPI1_ExchangeByte(writeData);
        CS_SetHigh();
        SPI1_Close();
        TempVariable = SPI_receiveData2 | SPI_receiveData<<8;
        TempVariable = (TempVariable >> 2);
        CurrentTemperature = TempVariable/4;
        ScaledTempF = ((CurrentTemperature*18)+320)/10; //convert to F
        ScaledTempHMI=ScaledTempF;


        //this function stops the output from getting too high as an over temp shut off
        if (ScaledTempHMI > SetTemperature)
            {
            Overtemp=1;
            HEATER_PWM_SetLow();//Setting low turns OFF the SCR
            EXHAUST_FAN_SetHigh();
            TMR2_Stop();
        }
        if (ScaledTempHMI < SetTemperature) {

            EXHAUST_FAN_SetLow();
            Overtemp = 0;
            
            if (DerivativeTime==1){ //check to see if its time to do math
                Error = SetTemperature - ScaledTempHMI;
                
                //Intergral = Intergral + Error;

                //check Intergral error to make sure it doesnt get too large
                //not really using the integral
                //if (Intergral >= 1023){Intergral=1023;}
                //if (Intergral <= -1023){Intergral=-1023;}           
                //Derivative = (Error - PreviousError);   

                //ki_term = (Intergral*Ki);
                kp_term = (Error*Kp);

                PIDoutput = kp_term; //+            

                if (PIDoutput <= 0){PIDoutput=0;}
                if (PIDoutput >=1000){PIDoutput=1000;}
                //PreviousError = Error;


                  //scale the output. In practice the min output for any physical change to happen is 150               
                 //PID=255-((PIDoutput*25)/100);
                 PIDinterm=((PIDoutput*16)/100);
                 PID = 160-PIDinterm;//
                 DerivativeTime=0;
                }//PID loop

        }     
   


        
        if (RoastFinished==0){

        }//roast NOT finished loop
        
        if (DisplayDelaytime==1 && RoastFinished == 0){
                
            // uncomment these lines
            printf("t");
            printf("%0.3u",Elapsed_Time);
           // __delay_ms(10);
            printf("a");
            printf("%0.3u",ScaledTempHMI);            
            //printf("%0.3u",ScaledTempHMI);    
             DisplayDelaytime=0;
         //PID=PIDLoop();
        }
        
        
        
        if (Elapsed_Time==Set_Time){//do times match? If so shut off heater
            //PID=255;
            HEATER_PWM_SetHigh();
            //Fanspeed=100;
            TMR2_Stop();
            //TMR1_StopTimer();                               
            //CoolingMode=1;
            //Cooling_Time=0;
            //RoastFinished=1;
            //Elapsed_Time=0;
            
        }//Roast Finished loop
        if (CoolingMode==1 && CoolingSecondsBit==1){

            //PID=255;
            HEATER_PWM_SetHigh();
            //Fanspeed=100;
            TMR2_Stop();
            RoastFinished=1;
            //Elapsed_Time=0;
            CoolingSecondsBit=0;
            DerivativeTime=0;
            
            //RPM=75;
        }//cooling mode loop    
        
    
    if (eusart1RxCount!=0){//is RX count not equal to 0? (ie is it 1)
     //begin sequence to read from the serial port
     //EUSART_Read_Text(buf,6);
     //make a button that prints out "FAN"
     //then compare and look for it

        
        EUSART_Read_Text(buf,4);
        //EUSART1_Write("0");
        COOL = strncmp (buf,"XCOL",4);
        //cooling mode on
        if (COOL==0){

         CoolingMode=1;

         memset(buf,0,8);//clear buffer after
        }

        CLEARTIME = strncmp (buf, "XZER",4);
        if (CLEARTIME==0){
          Elapsed_Time=0;
          printf("t");
          printf("%0.3u",Elapsed_Time);
          memset(buf,0,8);//clear buffer after
        }
        
        FIRSTCRACK = strncmp (buf, "XFCZ",4);
        if (FIRSTCRACK==0){
            FirstCrackTime=Elapsed_Time;
            //printf("z");
            //printf("%u",FirstCrackTime);
            Elapsed_Time=0;
            printf("t");
            printf("%0.3u",Elapsed_Time);
            
          memset(buf,0,4);//clear buffer after
        }        
//        TEMP_PLUS = strncmp (buf, "TE+",3);
//        if (TEMP_PLUS==0){
//            SetTemperature=SetTemperature+5;
//            //printf("Current Set Point Changed: =%u\n",SetTemperature);
//          memset(buf,0,3);//clear buffer after
//        }
//        //adjust Fan Speed
//        Fan_MINUS = strncmp (buf, "FE-",3);
//        if (Fan_MINUS==0){
//            Fanspeed=Fanspeed-5;
//            //printf("Current speed Changed: =%u\n",Fanspeed);
//          memset(buf,0,3);//clear buffer after
//        }        
//        Fan_PLUS = strncmp (buf, "FE+",3);
//        if (Fan_PLUS==0){
//            Fanspeed=Fanspeed+5;
//            //printf("Current speed Changed: =%u\n",Fanspeed);
//          memset(buf,0,3);//clear buffer after
//        }
//        //adjust rotation speed
//        Rot_MINUS = strncmp (buf, "RO-",3);
//        if (Rot_MINUS==0){
//            RPM=RPM-5;
//            //printf("Current Rotation Changed: =%u\n",RPM);
//          memset(buf,0,3);//clear buffer after
//        }        
//        Rot_PLUS = strncmp (buf, "RO+",3);
//        if (Rot_PLUS==0){
//            RPM=RPM+5;
//            //printf("Current Rotation Changed: =%u\n",RPM);
//            memset(buf,0,3);//clear buffer after
//        }
        Rot_ON = strncmp(buf, "XRON",4);
        if (Rot_ON==0){
            PWM6EN=1;
            ROTARTY_ON=1;
            //printf("Rotation ON\n");
            memset(buf,0,8);//clear buffer after           
        }
        Rot_OFF = strncmp(buf, "XROF",4);
        if (Rot_OFF==0){
            PWM6EN=0;
            ROTARTY_ON=0;
            //printf("Rotation OFF\n");
            memset(buf,0,8);//clear buffer after           
        }

    //command structure from display:
    //Snnn = temperature set point, character "S" followed by the 3 digits
    //Fnnn = Fan speed set point, character "F" followed by the 3 digits
    //Dnnn = Drum Speed set point, character "D" followed by the 3 digits
    //this then converts the number to ASCII and then we print
    //First function looks for temp set point    
        USART_TemperatureSP_Compare = strncmp(buf,"S",1);

        if (USART_TemperatureSP_Compare==0)
        {
            //memset(buf,0,3); //clear only the first 3 bytes
            //move things into a new buffer so we can get rid of the leading zeros
            IntBuffer[0]=buf[1];
            IntBuffer[1]=buf[2];
            IntBuffer[2]=buf[3];
            //then convert the buffer to an int;
            
            //***TEMP REMOVED ///***
            SetTemperature=atoi(IntBuffer);
            //then spit it back out in another text box. 
            //NextionSendNumber_command("n0.val=",val);
            //printf("New Setpoint: =%u\n",SetTemperature);
            //printf("I see you\n");
            memset(buf,0,4); //then clear the buffer after use
            memset(IntBuffer,0,4);
        }//end Set Point Look up
        
        //Look for Fan Speed Set Point
        
        USART_FanSPSP_Compare = strncmp(buf,"F",1);
        
        if (USART_FanSPSP_Compare ==0)
        {
            IntBuffer[0]=buf[1];
            IntBuffer[1]=buf[2];
            IntBuffer[2]=buf[3];
            Fanspeed=atoi(IntBuffer);
            //("New Fan Speed: =%u\n",Fanspeed);
            memset(buf,0,4); //then clear the buffer after use
            memset(IntBuffer,0,4);            
            
        }//end Fan Speed Look up
              
        //look up for Drum Speed
        USART_DrumSP_Compare = strncmp (buf,"D",1);
        
        if (USART_DrumSP_Compare==0)
        {
            IntBuffer[0]=buf[1];
            IntBuffer[1]=buf[2];
            IntBuffer[2]=buf[3];
            RPM=atoi(IntBuffer);
            //printf("New Drum Speed: =%u\n",RPM);
            memset(buf,0,4); //then clear the buffer after use
            memset(IntBuffer,0,4);            
        }//end Drum Speed look up
               
              
                
              
        //memset(eusart1RxBuffer,0,8);
        }//end rx loop
        //memset(eusart1RxBuffer,0,8);

    }//main loop end
}
/**
 End of File
*/

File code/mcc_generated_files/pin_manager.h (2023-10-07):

/**
  @Generated Pin Manager Header File

  @Company:
    Microchip Technology Inc.

  @File Name:
    pin_manager.h

  @Summary:
    This is the Pin Manager file generated using PIC10 / PIC12 / PIC16 / PIC18 MCUs

  @Description
    This header file provides APIs for driver for .
    Generation Information :
        Product Revision  :  PIC10 / PIC12 / PIC16 / PIC18 MCUs - 1.81.7
        Device            :  PIC16F18446
        Driver Version    :  2.11
    The generated drivers are tested against the following:
        Compiler          :  XC8 2.31 and above
        MPLAB 	          :  MPLAB X 5.45	
*/

/*
    (c) 2018 Microchip Technology Inc. and its subsidiaries. 
    
    Subject to your compliance with these terms, you may use Microchip software and any 
    derivatives exclusively with Microchip products. It is your responsibility to comply with third party 
    license terms applicable to your use of third party software (including open source software) that 
    may accompany Microchip software.
    
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
    IN NO EVENT WILL MICROCHIP BE LIABLE FOR ANY INDIRECT, SPECIAL, PUNITIVE, 
    INCIDENTAL OR CONSEQUENTIAL LOSS, DAMAGE, COST OR EXPENSE OF ANY KIND 
    WHATSOEVER RELATED TO THE SOFTWARE, HOWEVER CAUSED, EVEN IF MICROCHIP 
    HAS BEEN ADVISED OF THE POSSIBILITY OR THE DAMAGES ARE FORESEEABLE. TO 
    THE FULLEST EXTENT ALLOWED BY LAW, MICROCHIP'S TOTAL LIABILITY ON ALL 
    CLAIMS IN ANY WAY RELATED TO THIS SOFTWARE WILL NOT EXCEED THE AMOUNT 
    OF FEES, IF ANY, THAT YOU HAVE PAID DIRECTLY TO MICROCHIP FOR THIS 
    SOFTWARE.
*/

#ifndef PIN_MANAGER_H
#define PIN_MANAGER_H

/**
  Section: Included Files
*/

#include <xc.h>

#define INPUT   1
#define OUTPUT  0

#define HIGH    1
#define LOW     0

#define ANALOG      1
#define DIGITAL     0

#define PULL_UP_ENABLED      1
#define PULL_UP_DISABLED     0

// get/set RA2 procedures
#define RA2_SetHigh()            do { LATAbits.LATA2 = 1; } while(0)
#define RA2_SetLow()             do { LATAbits.LATA2 = 0; } while(0)
#define RA2_Toggle()             do { LATAbits.LATA2 = ~LATAbits.LATA2; } while(0)
#define RA2_GetValue()              PORTAbits.RA2
#define RA2_SetDigitalInput()    do { TRISAbits.TRISA2 = 1; } while(0)
#define RA2_SetDigitalOutput()   do { TRISAbits.TRISA2 = 0; } while(0)
#define RA2_SetPullup()             do { WPUAbits.WPUA2 = 1; } while(0)
#define RA2_ResetPullup()           do { WPUAbits.WPUA2 = 0; } while(0)
#define RA2_SetAnalogMode()         do { ANSELAbits.ANSA2 = 1; } while(0)
#define RA2_SetDigitalMode()        do { ANSELAbits.ANSA2 = 0; } while(0)

// get/set RB5 procedures
#define RB5_SetHigh()            do { LATBbits.LATB5 = 1; } while(0)
#define RB5_SetLow()             do { LATBbits.LATB5 = 0; } while(0)
#define RB5_Toggle()             do { LATBbits.LATB5 = ~LATBbits.LATB5; } while(0)
#define RB5_GetValue()              PORTBbits.RB5
#define RB5_SetDigitalInput()    do { TRISBbits.TRISB5 = 1; } while(0)
#define RB5_SetDigitalOutput()   do { TRISBbits.TRISB5 = 0; } while(0)
#define RB5_SetPullup()             do { WPUBbits.WPUB5 = 1; } while(0)
#define RB5_ResetPullup()           do { WPUBbits.WPUB5 = 0; } while(0)
#define RB5_SetAnalogMode()         do { ANSELBbits.ANSB5 = 1; } while(0)
#define RB5_SetDigitalMode()        do { ANSELBbits.ANSB5 = 0; } while(0)

// get/set RB6 procedures
#define RB6_SetHigh()            do { LATBbits.LATB6 = 1; } while(0)
#define RB6_SetLow()             do { LATBbits.LATB6 = 0; } while(0)
#define RB6_Toggle()             do { LATBbits.LATB6 = ~LATBbits.LATB6; } while(0)
#define RB6_GetValue()              PORTBbits.RB6
#define RB6_SetDigitalInput()    do { TRISBbits.TRISB6 = 1; } while(0)
#define RB6_SetDigitalOutput()   do { TRISBbits.TRISB6 = 0; } while(0)
#define RB6_SetPullup()             do { WPUBbits.WPUB6 = 1; } while(0)
#define RB6_ResetPullup()           do { WPUBbits.WPUB6 = 0; } while(0)
#define RB6_SetAnalogMode()         do { ANSELBbits.ANSB6 = 1; } while(0)
#define RB6_SetDigitalMode()        do { ANSELBbits.ANSB6 = 0; } while(0)

// get/set BUZZER aliases
#define BUZZER_TRIS                 TRISCbits.TRISC0
#define BUZZER_LAT                  LATCbits.LATC0
#define BUZZER_PORT                 PORTCbits.RC0
#define BUZZER_WPU                  WPUCbits.WPUC0
#define BUZZER_OD                   ODCONCbits.ODCC0
#define BUZZER_ANS                  ANSELCbits.ANSC0
#define BUZZER_SetHigh()            do { LATCbits.LATC0 = 1; } while(0)
#define BUZZER_SetLow()             do { LATCbits.LATC0 = 0; } while(0)
#define BUZZER_Toggle()             do { LATCbits.LATC0 = ~LATCbits.LATC0; } while(0)
#define BUZZER_GetValue()           PORTCbits.RC0
#define BUZZER_SetDigitalInput()    do { TRISCbits.TRISC0 = 1; } while(0)
#define BUZZER_SetDigitalOutput()   do { TRISCbits.TRISC0 = 0; } while(0)
#define BUZZER_SetPullup()          do { WPUCbits.WPUC0 = 1; } while(0)
#define BUZZER_ResetPullup()        do { WPUCbits.WPUC0 = 0; } while(0)
#define BUZZER_SetPushPull()        do { ODCONCbits.ODCC0 = 0; } while(0)
#define BUZZER_SetOpenDrain()       do { ODCONCbits.ODCC0 = 1; } while(0)
#define BUZZER_SetAnalogMode()      do { ANSELCbits.ANSC0 = 1; } while(0)
#define BUZZER_SetDigitalMode()     do { ANSELCbits.ANSC0 = 0; } while(0)

// get/set HEATER_PWM aliases
#define HEATER_PWM_TRIS                 TRISCbits.TRISC1
#define HEATER_PWM_LAT                  LATCbits.LATC1
#define HEATER_PWM_PORT                 PORTCbits.RC1
#define HEATER_PWM_WPU                  WPUCbits.WPUC1
#define HEATER_PWM_OD                   ODCONCbits.ODCC1
#define HEATER_PWM_ANS                  ANSELCbits.ANSC1
#define HEATER_PWM_SetHigh()            do { LATCbits.LATC1 = 1; } while(0)
#define HEATER_PWM_SetLow()             do { LATCbits.LATC1 = 0; } while(0)
#define HEATER_PWM_Toggle()             do { LATCbits.LATC1 = ~LATCbits.LATC1; } while(0)
#define HEATER_PWM_GetValue()           PORTCbits.RC1
#define HEATER_PWM_SetDigitalInput()    do { TRISCbits.TRISC1 = 1; } while(0)
#define HEATER_PWM_SetDigitalOutput()   do { TRISCbits.TRISC1 = 0; } while(0)
#define HEATER_PWM_SetPullup()          do { WPUCbits.WPUC1 = 1; } while(0)
#define HEATER_PWM_ResetPullup()        do { WPUCbits.WPUC1 = 0; } while(0)
#define HEATER_PWM_SetPushPull()        do { ODCONCbits.ODCC1 = 0; } while(0)
#define HEATER_PWM_SetOpenDrain()       do { ODCONCbits.ODCC1 = 1; } while(0)
#define HEATER_PWM_SetAnalogMode()      do { ANSELCbits.ANSC1 = 1; } while(0)
#define HEATER_PWM_SetDigitalMode()     do { ANSELCbits.ANSC1 = 0; } while(0)
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

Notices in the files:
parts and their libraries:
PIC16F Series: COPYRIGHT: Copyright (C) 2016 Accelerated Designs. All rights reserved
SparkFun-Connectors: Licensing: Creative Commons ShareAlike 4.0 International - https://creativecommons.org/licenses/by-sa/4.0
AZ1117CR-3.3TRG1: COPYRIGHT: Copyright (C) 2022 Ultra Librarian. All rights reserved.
